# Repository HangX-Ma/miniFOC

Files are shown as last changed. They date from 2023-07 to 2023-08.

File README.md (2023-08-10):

# miniFOC

This repository records my development of miniFOC. You can obtain the source files of the hardware and software in this repository.

## Introduction

This FOC driver board has three control mode, _Torque_, _Velocity_, _Angle_. You can control the motor accurately and smoothly using _**Voltage Control**_, because I haven't solved the _**Current Loop Control**_ problem.

Vofa+ can be used to control the motor conveniently. I also design a group of virtual keys to test the menu UI. You can find Vofa+ command configuration [vofa+.cmds.json](/Software/foc/vofa+.cmds.json) and [foc_debugger.tab.json](/Software/foc/foc_debugger.tab.json) that can assist you build up your debug platform quickly.

I have added a `Torque Ratchet Mode` under torque control. You can have a try.

> **NOTE:** <span style="color: #98C379; font-weight: bold;">`Software/foc/foc.ioc`</span> is only used for configuration reference.
>
> **NOTE:** :heavy_exclamation_mark: The hardware design is immature, which has some line sequence mistakes.

You can check the pin set via [cubemx-settings](assets/cubemx-settings.png). Vofa+ debugger tab can also be found in [assets/vofaplus.png](assets/vofaplus.png).

<div align="center">
    miniFOC design(concept), HangX-Ma
    <br>
    <font size="2" color="#999"><u>miniFOC design(concept), HangX-Ma</u></font>
    <br>
    <br>
</div>

<div align="center">
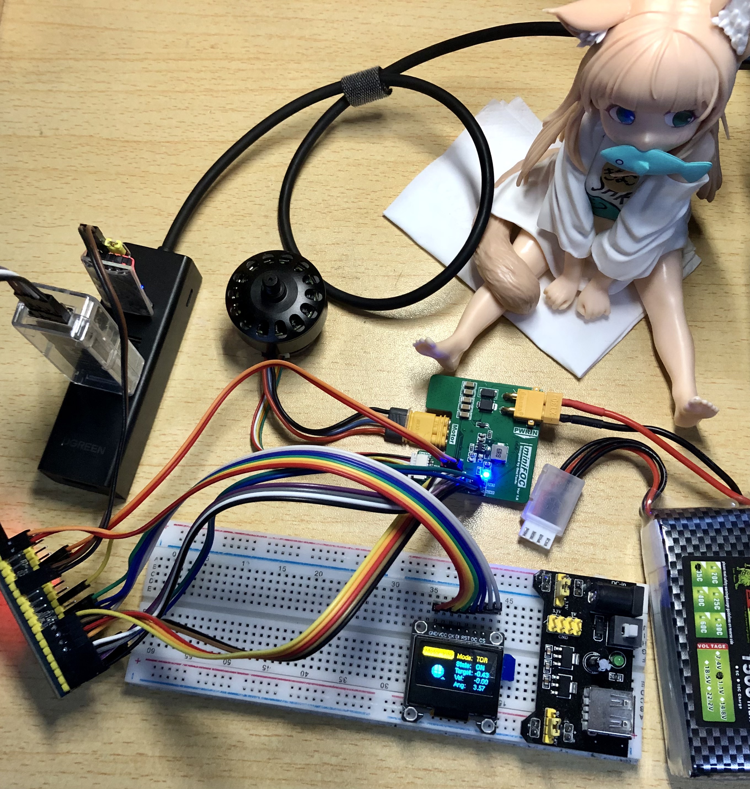
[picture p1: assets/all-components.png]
FOC board and other components, HangX-Ma
    
    <br>
    <font size="2" color="#999"><u>FOC board and other components, HangX-Ma</u></font>
    <br>
    <br>
</div>

> I will try to use sensor-less control strategy if the fundamental functions all perform well.

## Driver Parameters

| Item | Value |
| :---: | :---: |
| Input voltage range | 8 V ~ 40 V |
| Maximum current | 1.5 A |
| Serial port baud rate | 115200 |
| MCU | STM32F103C8T6, 64 KB flash, 20 KB RAM |
| OLED | SSD1306, 128 x 64, 7 wires SPI |
| Motor | 2808, KV900, 12 V|

## Environment

- **Serial Port Tool:** [Vofa+](https://www.vofa.plus/downloads/?v=7/17/2023)
- **OLED UI:** [WouoUI](https://github.com/RQNG/WouoUI), [uYanki/menu](https://github.com/uYanki/board-stm32f103rc-berial/tree/main/7.Example/hal/gui/u8g2/02_menu)
- **Dev Tools:** VSCode, CMake, OpenOCD, STLInk-v2, CMSIS-DAPv2, STM32CubeMX
- **Debugger:** Cortex-Debug
- **Library:** [u8g2](https://github.com/olikraus/u8g2), [Qfplib-M3](https://www.quinapalus.com/qfplib-m3.html)

## Features

- [x] Using space vector pulse width modulation
- [x] Torque control without current sensor
- [x] Rotational speed closed loop control
- [x] Rotation angle closed loop control
- [ ] Torque control with current sensor
- [x] Smooth UI that can be controlled by virtual keys currently via Vofa

## FOC Application

- _**Torque Normal Mode**_

    &emsp;&emsp; Under torque control, you can set the `target torque` and `Kp` to adjust torque feedback force.

- _**Torque Ratchet Mode**_

    &emsp;&emsp; Under torque control, the motor will act like a ratchet.

    &emsp;&emsp; You can change `Kp` to adjust the stiffness.

- _**Torque Rebound Mode**_

    &emsp;&emsp; Under torque control, the motor will rebound to the specific angle.

    &emsp;&emsp; You can set the angle or change the rebound force by adjusting the `Kp` value.

- _**Torque Damp Mode**_

    &emsp;&emsp; Under torque control, the motor will act like a knob with damp.

    &emsp;&emsp; If you increase the `target torque` value, the damp will increase.

    &emsp;&emsp; If you increase the `Kd` value, the knob will become smoother.

## Problem Found

- SPI output pins sequence needs to be `CS`, `SCLK`, `MISO`, `MOSI`.
- Magnetic attached to motor will affect the motor itself, my friend suggests me to use sensorless control strategy.
- More power ports need to be reserved, such as `GND`, `3V3`.
- SPI OLED ports sequence needs to be `GND`, `VCC`, `SCK`, `MOSI`, `RST`, `DC`, `CS`.
- `nFault` pin of the DRV8313 needs to be controlled and monitored by the MCU. Currently, only unplugging battery can release the DRV8313 off the fault state.

## Development Logs

### 2023-08-10

- Fix the problem caused by TIM3 configuration, which will lead to OLED abnormal display.
    > I remove the `LL_TIM_CC_EnableChannel` function, which actually used in capture/compare mode! It is a coincidence that the OLED pins happened to be coincided with the configured channel.
- Change current sampling to three phases version.
- Move FOC state update in ADC1 DMA transfer complete interrupt. This will fit the current sampling demand and meet the inner ring frequency requirements.
- Current sensors are combined with a strange 100 Hz sine- wave noise. I cannot fix it currently.

<div align="center">
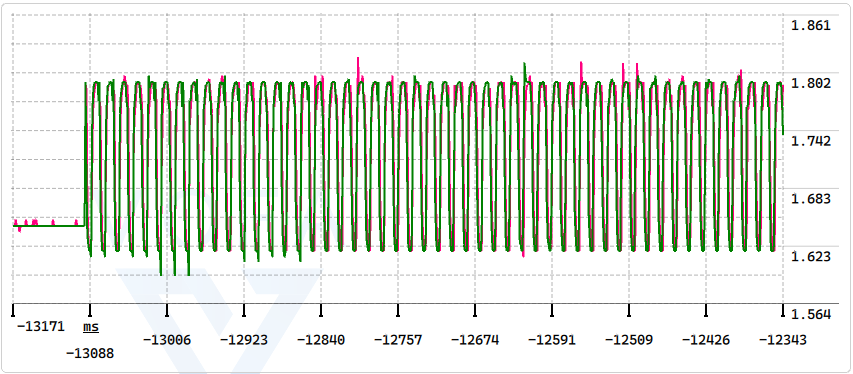
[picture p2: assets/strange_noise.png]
Strange 100 Hz sine-wave current noise , HangX-Ma
    
    <br>
    <font size="2" color="#999"><u>Strange 100 Hz sine-wave current noise
, HangX-Ma</u></font>
</div>

### 2023-08-06 to 2023-08-07

- Reconstruct GUI logic to support mult-level menu and motor app mode switch.
- Enhance the MainUI animation logic to follow the actual angle position.
- Add **Damp Mode**.
- Add damp feeling control for **Rebound Mode**
- Add _**High Pass Filter**_ but it is discarded afterwards because it filters out the useful information.

### 2023-08-05

- Update the voltage control with with current estimation and Back-EMF compensation. I take a reference to SimpleFOC, [Torque control using voltage](https://docs.simplefoc.com/voltage_torque_mode).

<div align="center">
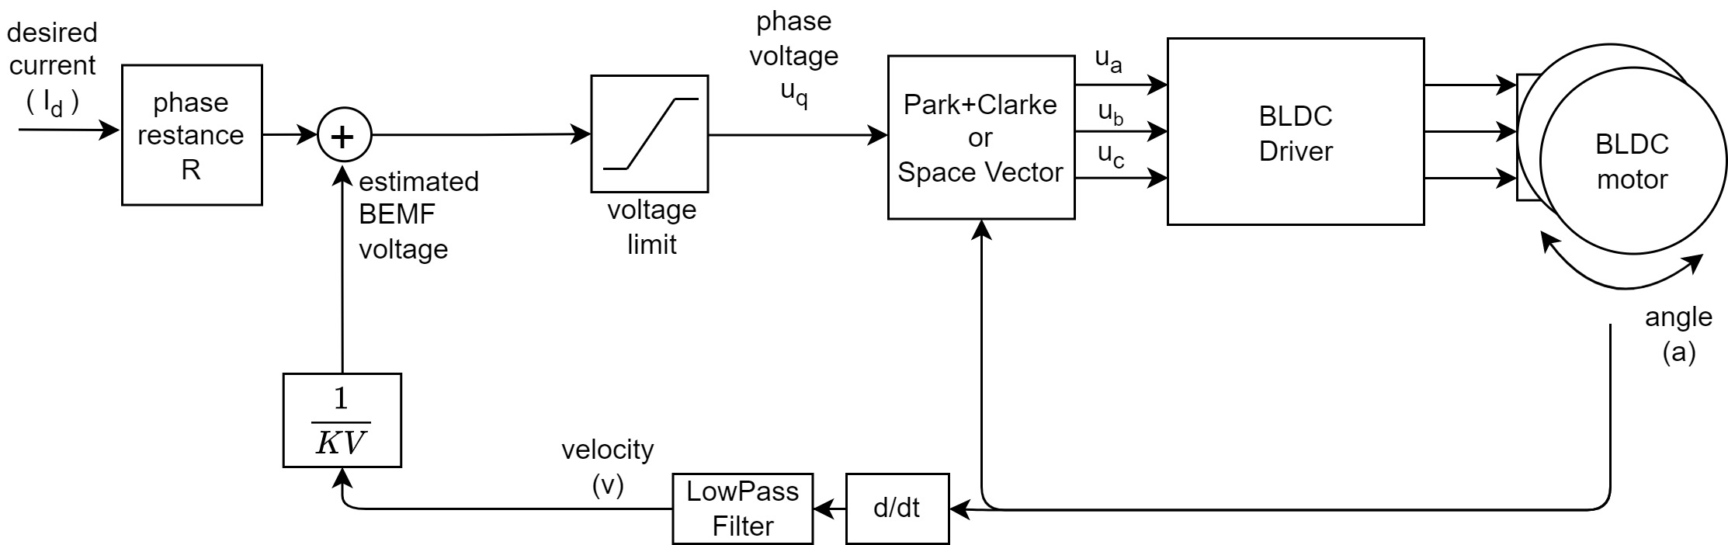
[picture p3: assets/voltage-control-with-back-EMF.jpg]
Voltage control with current estimation and Back-EMF compensation , HangX-Ma
    
    <br>
    <font size="2" color="#999"><u>Voltage control with current estimation and Back-EMF compensation
, HangX-Ma</u></font>
</div>

### 2023-08-01 to 2023-08-04

- Add OLED smooth menu UI and make control relationship between UI and motor. The motor information such that **Motor Control Mode**, **Motor State**, **Control Target**, **Shaft Velocity**, **Shaft Angle**. The animation in _MainUI_ will show you the state of motor!

### 2023-07-31

- Find a project procedure problem that you must reconfirm the encoder direction if you reassemble your hardware.
- Only low speed mode can support the motor position rebound test. Otherwise, the motor will be damaged.
    > :sob: My motor seems to be damaged. (Update: It recovered!)
- Replace the PWMA current sensor and the current loop start to work.
    > I finally only give Q and D with Kp = 0.6 and make the current loop work. But actually current loop version performs not as good as non current loop version.
- Torque needs to be greater than 0.6 under current loop control.
- Add ratchet mode under torque control.

### 2023-07-30

- Add current sense monitor feedback, thus, creating a current control loop.
    > :x: Current phase sequence is necessary to be identified. I haven't solve the it. Motor can not work when current feedback added.
- Add _Torque Control_ part, reconstruct the control logic and delete some abundant codes.

### 2023-07-29

- Add velocity control loop and fix the jitter problem.
- Add position control loop.
- Add motion switch function and fix the motor jump problem when control type switches.
- Remove integral part in _Angle Control_. Only proportional part is left.
    > :heavy_exclamation_mark: Integral part actually causes serious overshoot problem and affects the system response speed.

### 2023-07-28

- Attach the magnetic with shaft sleeve, sticking it on the shaft.
- Remake an encoder board because previous one seems to be damaged.
- Ensure the UVW sequence of the Motor.
- <span style="color: #98C379; font-weight: bold;">[Pass TEST3]:</span> Open loop position control test passes.
- Add `printf` redirection code.
- Add sensor alignment code: Identify the sensor direction, pole pairs and calculate the zero electrical angle offset.
    > The code will be trapped into a rabbit hole if the motor rotates not fluently. So check the serial output first!

### 2023-07-26

- Add OLED menu base code.

### 2023-07-25

- INA199x1 has been configured successfully. I use TIM3 to generate update event to trigger ADC1 to start multi-channel conversion. The conversion result will be carried by DMA and send to specific address.
- Add `get_RS_current` function that can conveniently return the rotor and stator current (Id and Iq). I also write a test code for it.

### 2023-07-24

- SC60228DC magnetic encoder works well. I brought _5 mm x 2 mm (d x h)_ magnetic but can not stick it to the motor bearing using hot-melt adhesive. I will use AB glue instead.
    > Waiting for essential materials again~

### 2023-07-23

- Add SVPWM control module and change PWM to center aligned mode.
- <span style="color: #98C379; font-weight: bold;">[Pass TEST2]:</span> SVPWM control test passes.

### 2023-07-22

- <span style="color: #98C379; font-weight: bold;">[Pass TEST1]:</span> Direct given PWM can successfully drive BLDC motor.
- Fix transmission error of SPI2, which is linked to magnetic encoder. But I forget to buy the magnetic, so fully check hasn't been done.

### 2023-07-21

- Add [u8g2](https://github.com/olikraus/u8g2) OLED library and add OLED demo code.
    >
    > - :x: OLED can not display normally, which needs further checking.
    > - :heavy_check_mark: Remove SPI1 DMA and the SPI OLED can display normally using u8g2.

- Reconstruct PWMx configurations and merges it into BLDC configurations.
- Add BLDC motor tests for checking different BLDC motor working conditions.
- Add USART control to start or stop BLDC motor.
- Driver board has been prepared.

### 2023-07-19

- Add [Qfplib-M3](https://www.quinapalus.com/qfplib-m3.html) float-point library and it works well!
    > I use cortex-debug plugin and it shows that Qfplib-M3 is visibly faster than software float-point calculation.
- Add Vofa+ communication protocol and configure USART1.
    >
    > - :question: Cough... It seems that my CH340 serial communication device breaks down. Need further checking.
    > - :heavy_check_mark: I use logic analyzer to capture output of _**PB6(Tx)**_ and it actually gives me different waveforms, which means that the CH340 is actually broken.

### 2023-07-18

- Change SPI mode to **(Receive Only Master)** and finish the SC60228DC software logic.
    > Use OOP concept to write SC60228DC, use method in `g_encoder` can satisfy the user's need.

### 2023-07-17

- :book: Create a mind map about _miniFOC_ design.
- :rocket: Finish the board design but haven't check the details. Prepare for further checking and BOM selections.
    > :heavy_check_mark: BOM and board have been checked. Waiting for all materials to arrive.
- Remove `TIM1_CH1N`, `TIM1_CH2N`, `TIM1_CH3N` settings， because they are not used in this driver.

### 2023-07-15

- :x: I tried to use proteus 8.15 to develop the software using online simulation, but the NMOS in proteus performed abnormally. I will use **Logic Analyzer** instead and design the modular board.

## License

Apache License Version 2

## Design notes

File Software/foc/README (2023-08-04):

# SPDX-License-Identifier: Apache-2.0
# (C) Copyright 2023
# HangX-Ma, contour.9x@gmail.com

Warning:
========

1. Don't use the 'Makefile' in the root directory. It is generated
   by STM32CubeMX, which is not maintained.

2. Don't use the STM32CubeMX directly. It only gives you a reference
   to my configurations.

3. Only low speed mode can support the motor position rebound test.
   Otherwise, the motor will be damaged.

Note:
========

1. Wait until the LED off and then start the motor. Otherwise, you
   may cause an undefined situation.

2. If the motor suddenly stops, it may be now protected by the DRV8313,
   you need to pull off the battery to release the fault state of DRV8313.

3. Torque needs to be greater than 0.6 under current loop control

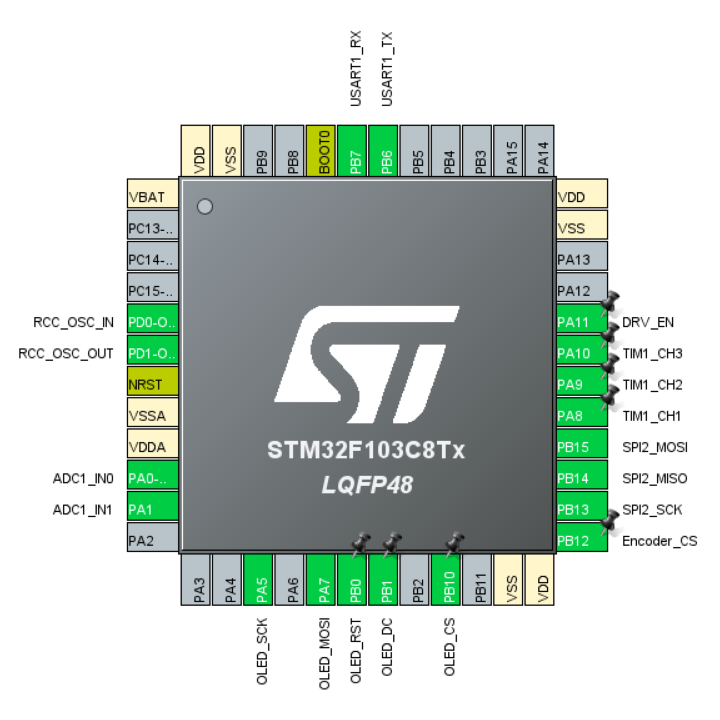
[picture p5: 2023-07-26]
assets/cubemx-settings.png

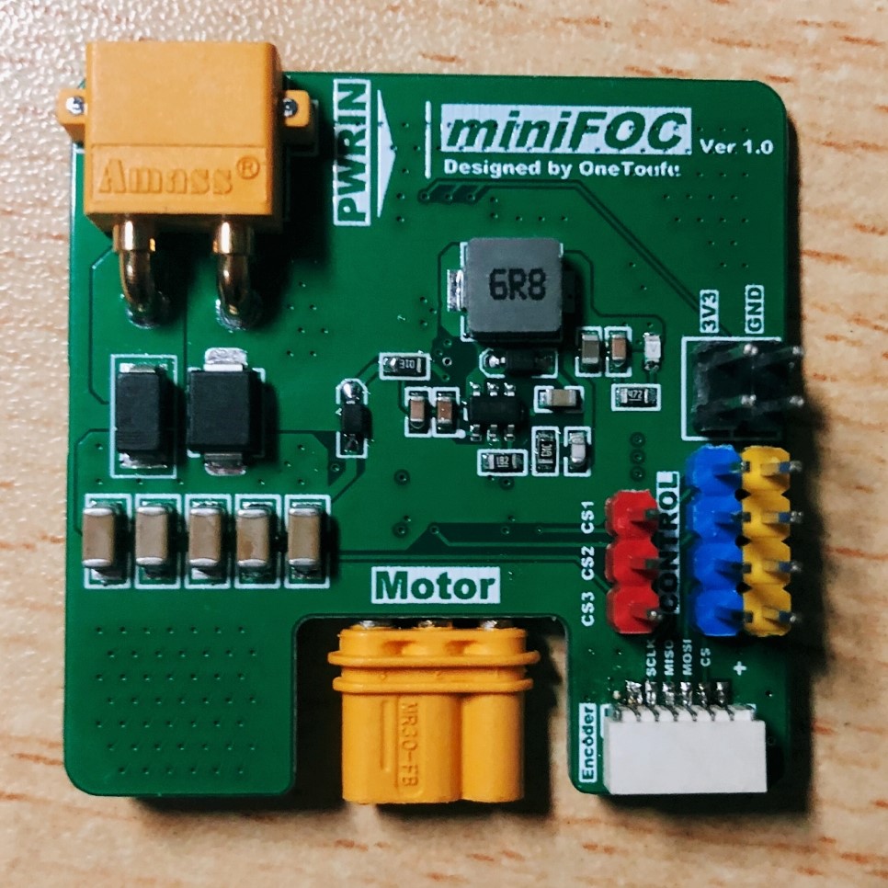
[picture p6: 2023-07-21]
assets/bldc-board.png

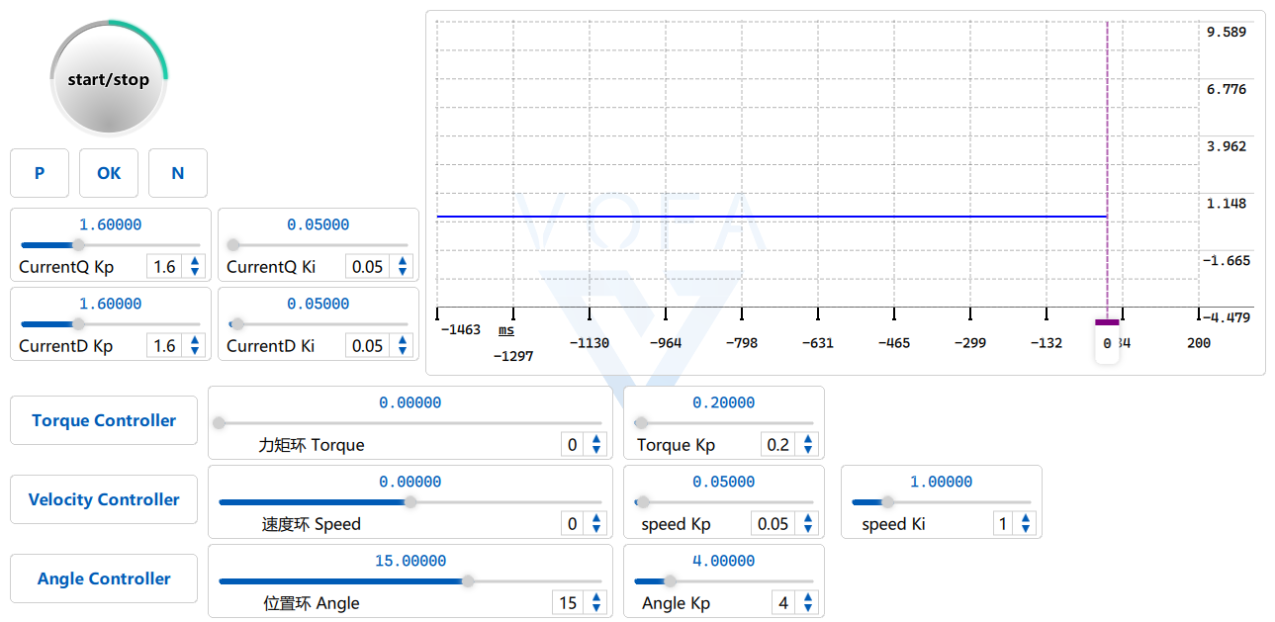
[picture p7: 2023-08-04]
assets/vofaplus.png

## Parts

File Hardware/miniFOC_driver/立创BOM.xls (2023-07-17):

购买类型 | 商品编号 | 物料编码 | 商品分类 | 名称 | 商品型号 | 品牌 | 封装规格 | 单个毛重 | 购买数量 | 商品单价 | 金额
常规 | C431092 |  | 插头 | AMASS(艾迈斯)航模插头 卧式弯脚 XT30PW-M公头 袋装 | XT30PW-M | AMASS(艾迈斯) | - | 0.001296000 | 3 | ￥2.22 | ￥6.66
常规 | C30926 |  | 贴片电容(MLCC) | 100nF ±10% 50V 编带 | 0603B104K500NT | FH(风华) | 0603 | 0.000030000 | 100 | ￥0.014054 | ￥1.41
常规 | C77572 |  | 贴片电容(MLCC) | 470nF ±10% 50V 编带 | 0603B474K500NT | FH(风华) | 0603 | 0.000030000 | 50 | ￥0.092223 | ￥4.61
常规 | C14665 |  | 贴片电容(MLCC) | 100pF ±5% 50V 编带 | CC0603JRNPO9BN101 | YAGEO(国巨) | 0603 | 0.000029000 | 100 | ￥0.013901 | ￥1.39
常规 | C100042 |  | 贴片电容(MLCC) | 10nF ±10% 50V 编带 | CC0603KRX7R9BB103 | YAGEO(国巨) | 0603 | 0.000023000 | 100 | ￥0.012596 | ￥1.26
常规 | C96446 |  | 贴片电容(MLCC) | 10uF ±20% 25V 编带 | CL10A106MA8NRNC | SAMSUNG(三星) | 0603 | 0.000035000 | 20 | ￥0.148527 | ￥2.97
常规 | C883598 |  | 贴片电容(MLCC) | 100uF ±20% 10V 编带 | GRM31CR61A107MEA8L | muRata(村田) | 1206 | 0.000045000 | 10 | ￥1.2912 | ￥12.91
常规 | C2929944 |  | 肖特基二极管 | SS54 编带 | SS54 | CJ(江苏长电/长晶) | SMAG | 0.000500000 | 5 | ￥0.598284 | ￥2.99
常规 | C726872 |  | 瞬态抑制二极管(TVS) | SMBJ28CA 编带 | SMBJ28CA | TWGMC(台湾迪嘉) | SMB(DO-214AA) | 0.000152000 | 10 | ￥0.211826 | ￥2.12
常规 | C22624 |  | 肖特基二极管 | 40V 1A 600mV@1A 编带 | B5819WS | CJ(江苏长电/长晶) | SOD-323 | 0.000029000 | 20 | ￥0.186073 | ￥3.72
常规 | C325965 |  | 功率电感 | 6.8uH ±20% 编带 | SLO0530H6R8MTT | Sunltech(韩国顺磁) | SMD | 0.000340000 | 5 | ￥0.838292 | ￥4.19
常规 | C99873 |  | 插头 | AMASS(艾迈斯)锂电池三芯电源连接器公头MR30-M 2件套 袋装 | MR30-M | AMASS(艾迈斯) | - | 0.001950000 | 2 | ￥1.79 | ￥3.58
常规 | C23162 |  | 贴片电阻 | 厚膜电阻 4.7kΩ ±1% 100mW 编带 | 0603WAF4701T5E | UNI-ROYAL(厚声) | 0603 | 0.000023000 | 100 | ￥0.006624 | ￥0.66
常规 | C4177 |  | 贴片电阻 | 厚膜电阻 1.8kΩ ±1% 100mW 编带 | 0603WAF1801T5E | UNI-ROYAL(厚声) | 0603 | 0.000023000 | 100 | ￥0.006187 | ￥0.62
常规 | C25804 |  | 贴片电阻 | 厚膜电阻 10kΩ ±1% 100mW 编带 | 0603WAF1002T5E | UNI-ROYAL(厚声) | 0603 | 0.000023000 | 100 | ￥0.005512 | ￥0.55
常规 | C136593 |  | 贴片电阻 | 1MΩ ±1% 100mW 编带 | RS-03K1004FT | FH(风华) | 0603 | 0.000030000 | 100 | ￥0.004880 | ￥0.49
常规 | C728271 |  | 贴片电阻 | 10mΩ ±1% 500mW 编带 | PA0805FRE470R01L | YAGEO(国巨) | 0805 | 0.000030000 | 10 | ￥0.368704 | ￥3.69
常规 | C92482 |  | 电机驱动芯片 | 无刷直流BLDC电机驱动芯片 60V 编带 | DRV8313PWPR | TI(德州仪器) | TSSOP-28-EP | 0.000261000 | 2 | ￥13.08 | ￥26.16
常规 | C97643 |  | DC-DC电源芯片 | 降压型 编带 | ME3116AM6G | MICRONE(南京微盟) | SOT-23-6 | 0.000055000 | 5 | ￥0.8500 | ￥4.25
常规 | C59135 |  | 电流感应放大器 | INA199A1DCKR 编带 | INA199A1DCKR | TI(德州仪器) | SOT-323-6 | 0.000070000 | 10 | ￥1.99 | ￥19.90

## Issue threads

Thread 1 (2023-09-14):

Hello

Candas1, 2023-09-14:
Hello,

Very insteresting project.
Are you in the SimpleFOC community ?
I am currently checking if Qfplib would help getting FOC to run faster and just saw you are using it.
Do you have any feedback ?

Thanks in advance.

HangX-Ma, 2023-09-14:
I'm glad you are interested in my miniFOC project. I'm not a member of Simple FOC community but I actually learn a lot techniques and knowledge from it. I once majored in EE when in undergraduate. Doing this project was purely out of personal interest. Qfplib works well in Cortex-M3 series chips. I think TI's IQmath has widely used in such chips that has no hardware float calculation capability. I just want to find a math library to substitute it. Actually, Qfplib works well. I used to debug my project and this math library visibly speeded up the calculation process, though not accurately as using those timing lib. I hope my answer can assist your further study and work. -v-

Candas1, 2023-09-15:
Thank you.
I will try it, it seems Qfplib can be used to substitute match operators without changing the code ([blog post](https://lupyuen.github.io/articles/stm32-blue-pill-shrink-your-math-libraries-with-qfplib)).

I recently proposed [this](https://github.com/simplefoc/Arduino-FOC/pull/309), maybe this is also useful for you.

SimpleFOC could probably run on your hardware.

HangX-Ma, 2023-09-15:
Great posts! Thanks for your suggestion. I think they will increase my understanding of Qfplib and optimize my firmware.

Candas1, 2023-09-18:
You have 3 shunts, you could also only use the 2 phase currents of the phases with lowest duty cycle and do the foc with 2 phase currents only.

That would prevent issues at high duty cycle.

HangX-Ma, 2023-09-18:
> You have 3 shunts, you could also only use the 2 phase currents of the phases with lowest duty cycle and do the foc with 2 phase currents only.
>
> That would prevent issues at high duty cycle.

I used to use the two phases version, but I encountered with the current phase sequence problem. Three phases control version cloud give me a chance to change the current phase sequence conveniently. Finally, I found that maybe my hardware design has some subtle mistakes that introduces noise into the current sense module. I didn't solve this problem. So this firmware version only uses the voltage control method.

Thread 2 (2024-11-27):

Interest with your project posible step/dir input??

artayasa, 2024-11-27:
Hi mate i want make this, i have all, but i want make a high power, i have it with opto isolated. But it need pwm for hin and lin active low. Is posible??

artayasa, 2024-11-30:
> > Hi mate i want make this, i have all, but i want make a high power, i have it with opto isolated. But it need pwm for hin and lin active low. Is posible??
>
> Hi, I haven't tested this board limitation. But I think this project may not suitable because the motor current may overflow the tolerance value. And drv8313 may be not a good choice for high power situation.

Owhh is still used drv ohh ok

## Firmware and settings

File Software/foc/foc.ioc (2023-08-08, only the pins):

Mcu.UserName=STM32F103C8Tx
PA0-WKUP.Signal=ADCx_IN0
PA1.Signal=ADCx_IN1
PA10.Signal=S_TIM1_CH3
PA11.GPIO_Label=DRV_EN
PA11.Signal=GPIO_Output
PA2.Signal=ADCx_IN2
PA5.GPIO_Label=OLED_SCK
PA5.Signal=SPI1_SCK
PA7.GPIO_Label=OLED_MOSI
PA7.Signal=SPI1_MOSI
PA8.Signal=S_TIM1_CH1
PA9.Signal=S_TIM1_CH2
PB0.GPIO_Label=OLED_RST
PB0.Signal=GPIO_Output
PB1.GPIO_Label=OLED_DC
PB1.Signal=GPIO_Output
PB10.GPIO_Label=OLED_CS
PB10.Signal=GPIO_Output
PB12.GPIO_Label=Encoder_CS
PB12.Signal=GPIO_Output
PB13.Signal=SPI2_SCK
PB14.Signal=SPI2_MISO
PB15.Signal=SPI2_MOSI
PB6.Signal=USART1_TX
PB7.Signal=USART1_RX
PD0-OSC_IN.Signal=RCC_OSC_IN
PD1-OSC_OUT.Signal=RCC_OSC_OUT

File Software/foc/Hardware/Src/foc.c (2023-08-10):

#include "foc.h"
#include "foc_app.h"
#include "config.h"
#include "bldc_config.h"
#include "encoder.h"
#include "qfplib-m3.h"
#include "vofa_usart.h"
#include "led.h"
#include "pid.h"
#include <math.h>
#include "current_monitor.h"

#include "stm32f1xx_ll_utils.h"
#include "stm32f1xx_ll_tim.h"

FOC g_foc;

// normalize angle to range [0, 2PI]
static float normalize_angle(float angle) {
    float _fmod = fmodf(angle, _2PI);
    return _fmod >= 0 ? _fmod : qfp_fadd(_fmod, _2PI);
}

static float get_electrical_angle(float shaft_angle) {
    return normalize_angle(
        qfp_fsub(
            qfp_fmul(shaft_angle, (float)g_foc.property_.pole_pairs),
            g_foc.property_.zero_electrical_angle_offset
        )
    );
}


static void set_phase_voltage(float Uq, float Ud, float e_angle) {
    float U_ref, U_alpha, U_beta;
    float T0, T1, T2;
    float Ta, Tb, Tc;
    uint8_t sector;

    // invert park
    U_alpha = qfp_fsub(qfp_fmul(Ud, qfp_fcos(e_angle)), qfp_fmul(Uq, qfp_fsin(e_angle)));
    U_beta  = qfp_fadd(qfp_fmul(Ud, qfp_fsin(e_angle)), qfp_fmul(Uq, qfp_fcos(e_angle)));

    // normalized U_ref range between [-1, 1]
    U_ref = qfp_fdiv(qfp_fsqrt(qfp_fadd(qfp_fmul(U_alpha, U_alpha), qfp_fmul(U_beta, U_beta))), MOTOR_VM);

    // We need to calculate the rotor's electric angle. THe rotor is _PI_2 head of the stator.
    if (Uq > 0) {
        e_angle = normalize_angle(qfp_fadd(e_angle, _PI_2));
    } else {
        e_angle = normalize_angle(qfp_fsub(e_angle, _PI_2));
    }

    // SVPWM maximum distortion-free rotation voltage vector: sqrt(3)/3
    // The inscribed circle of a hexagon.
    if (U_ref > 0.577f) {
        U_ref = 0.577f;
    }
    if (U_ref < -0.577f) {
        U_ref = -0.577f;
    }

    // calculate the sector
    sector = (uint8_t) qfp_fdiv(e_angle, _PI_3) + 1;

    // calculate the neighbour voltage vector action time

    float m = qfp_fmul(_SQRT3, U_ref);
    T1 = qfp_fmul(m, qfp_fsin(qfp_fsub(qfp_fmul(sector, _PI_3), e_angle)));
    T2 = qfp_fmul(m, qfp_fsin(qfp_fsub(e_angle, qfp_fmul(qfp_fsub(sector, 1.0f), _PI_3))));
    T0 = qfp_fsub(qfp_fsub(1.0f, T1), T2);

    float T0_2 = qfp_fdiv(T0, 2.0f);

    switch(sector)
    {
        case 1:
            Ta = qfp_fadd(qfp_fadd(T1, T2), T0_2);
            Tb = qfp_fadd(T2, T0_2);
            Tc = T0_2;
            break;
        case 2:
            Ta = qfp_fadd(T1, T0_2);
            Tb = qfp_fadd(qfp_fadd(T1, T2), T0_2);
            Tc = T0_2;
            break;
        case 3:
            Ta = T0_2;
            Tb = qfp_fadd(qfp_fadd(T1, T2), T0_2);
            Tc = qfp_fadd(T2, T0_2);
            break;
        case 4:
            Ta = T0_2;
            Tb = qfp_fadd(T1, T0_2);
            Tc = qfp_fadd(qfp_fadd(T1, T2), T0_2);
            break;
        case 5:
            Ta = qfp_fadd(T2, T0_2);
            Tb = T0_2;
            Tc = qfp_fadd(qfp_fadd(T1, T2), T0_2);
            break;
        case 6:
            Ta = qfp_fadd(qfp_fadd(T1, T2), T0_2);
            Tb = T0_2;
            Tc = qfp_fadd(T1, T0_2);
            break;
        default:  // possible error state
            Ta = 0.0f;
            Tb = 0.0f;
            Tc = 0.0f;
    }
    g_bldc.set_pwm_a_duty((uint32_t)qfp_fmul(Ta, (float)PWM_RELOAD_PERIOD));
    g_bldc.set_pwm_b_duty((uint32_t)qfp_fmul(Tb, (float)PWM_RELOAD_PERIOD));
    g_bldc.set_pwm_c_duty((uint32_t)qfp_fmul(Tc, (float)PWM_RELOAD_PERIOD));
}

// Encoder DIR needs to be reserved. Otherwise, the FOC will stick into one
// position if you call any function that rely on the encoder feedback.
#define ESTIMATE_ENCODER_DIR    (1)
static void align_sensor(void) {
    // electrical direction needs to be correspond to the mechanical angle
    float e_angle; // electrical angle
    float forward_angle, back_angle, delta_abs_angle; // mechanic angle

    printf("\n[Motor]: Start sensor alignment...\r\n");

    // we need to start pwm output first
    LED_STATE_ON();
    g_bldc.start_pwm();
    LL_mDelay(500);

    /* We want to ensure the sensor direction and the pole pairs number */
    // forward 2PI electrical angle
    for(int i = 0; i <= 100; i++) {
        e_angle = qfp_fadd(_3PI_2, qfp_fdiv(qfp_fmul(_2PI, i), 100.0f));
        g_foc.set_phase_voltage(SENSOR_ALIGN_VOLTAGE, 0, e_angle);
        LL_mDelay(20);
    }
    forward_angle = g_encoder.get_angle();

    // turn back
    for(int i = 100; i >= 0; i--) {
        e_angle = qfp_fadd(_3PI_2, qfp_fdiv(qfp_fmul(_2PI, i), 100.0f));
        g_foc.set_phase_voltage(SENSOR_ALIGN_VOLTAGE, 0, e_angle);
        LL_mDelay(20);
    }
    back_angle = g_encoder.get_angle();

    printf("[Motor]: Forward angle is degree %d\r\n", (int)qfp_fmul(qfp_fdiv(forward_angle, _PI), 180.0f));
    printf("[Motor]: Back angle is degree %d\r\n", (int)qfp_fmul(qfp_fdiv(back_angle, _PI), 180.0f));

    // Try to stop motor at zero point
    g_foc.set_phase_voltage(0, 0, 0);
    LL_mDelay(200);

    // Motor moves none, which indicates motor error.
    delta_abs_angle = abs(qfp_fsub(forward_angle, back_angle));
    if(( delta_abs_angle < 0.02f)) {
        printf("[Motor]: Abnormal state. Please check encoder or motor.\n");
        LED_STATE_OFF();
        // stop pwm output. Motor will be stopped and this also can avoid emergency situation
        g_bldc.stop_pwm();
        return;
    }

#if ESTIMATE_ENCODER_DIR
    //* determine the sensor direction
    if(forward_angle < back_angle) {
        printf("[Motor]: Encoder dir is CCW\r\n");
        g_encoder.dir_ = CCW;
    }
    else {
        printf("[Motor]: Encoder dir is CW\r\n");
        g_encoder.dir_ = CW;
    }
#else
    g_encoder.dir_ = CCW;
#endif

#if ESTIMATE_POLE_PAIRS
    //* calculate motor pole pairs
    printf("[Motor]: Pole pairs checking...\r\n");
    // 0.5 is arbitrary number it can be lower or higher!
    // If the default pole pairs isn't correct, we use the calculated one!
    if( abs(qfp_fsub(qfp_fmul(delta_abs_angle, g_foc.property_.pole_pairs), _2PI)) > 0.5f ) {
        g_foc.property_.pole_pairs = qfp_fadd(qfp_fdiv(_2PI, delta_abs_angle), 0.5f);
        if (g_foc.property_.pole_pairs > MOTOR_POLE_PAIRS + 1 || g_foc.property_.pole_pairs < MOTOR_POLE_PAIRS - 1) {
            g_foc.property_.pole_pairs = MOTOR_POLE_PAIRS;
            printf("[Motor]: Estimate pole pairs error.\n");
            LED_STATE_OFF();
            // stop pwm output. Motor will be stopped and this also can avoid emergency situation
            g_bldc.stop_pwm();
            return;
        } else {
            printf("[Motor]: Estimated pole pairs = %d\r\n", g_foc.property_.pole_pairs);
        }
    } else {
        printf("[Motor]: Ok!\r\n");
    }
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

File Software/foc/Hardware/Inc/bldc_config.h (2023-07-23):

/**
 * @file bldc_config.h
 * @author HangX-Ma (contour.9x@gmail.com)
 * @brief BLDC essential configurations
 * @version 0.1
 * @date 2023-07-21
 * @ref https://github.com/simplefoc/Arduino-FOC-drivers/tree/master/src/encoders/sc60228
 * @ref https://blog.csdn.net/weixin_43593122/article/details/119253544
 *
 * @copyright Copyright (c) 2023
 *
 * Licensed under the Apache License, Version 2.0 (the "License");
 * you may not use this file except in compliance with the License.
 * You may obtain a copy of the License at
 *
 *    http://www.apache.org/licenses/LICENSE-2.0
 *
 * Unless required by applicable law or agreed to in writing, software
 * distributed under the License is distributed on an "AS IS" BASIS,
 * WITHOUT WARRANTIES OR CONDITIONS OF ANY KIND, either express or implied.
 * See the License for the specific language governing permissions and
 * limitations under the License.
 */

#ifndef __BLDC_CONFIG__H__
#define __BLDC_CONFIG__H__

#include "utils.h"

#define BLDC_DRV_EN_GPIO_PORT       GPIOA
#define BLDC_DRV_EN_PIN             LL_GPIO_PIN_11

#define BLDC_PWMx_GPIO_PORT         GPIOA
#define BLDC_PWMA_PIN               LL_GPIO_PIN_8
#define BLDC_PWMB_PIN               LL_GPIO_PIN_9
#define BLDC_PWMC_PIN               LL_GPIO_PIN_10

typedef struct BLDC {
    void (*set_pwm_a_duty)(uint32_t);
    void (*set_pwm_b_duty)(uint32_t);
    void (*set_pwm_c_duty)(uint32_t);
    void (*start_pwm)(void);
    void (*stop_pwm)(void);
} BLDC;
extern BLDC g_bldc;

void bldc_init();

#endif  //!__BLDC_CONFIG__H__

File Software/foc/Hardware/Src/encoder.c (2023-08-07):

#include "encoder.h"
#include "delay.h"
#include "qfplib-m3.h"
#include "pid.h"

#include "stm32f1xx_ll_utils.h"
#include "stm32f1xx_ll_spi.h"
#include "stm32f1xx_ll_gpio.h"
#include "stm32f1xx_ll_bus.h"


Encoder g_encoder;
typedef struct {
    BOOL error_check;   // indicate the SC60228 state
    BOOL parity_check;  // if the received data has error or not
} data_check_t;

static data_check_t data_check = {
    .error_check = FALSE,
    .parity_check = FALSE,
};


static float raw_angle_data_prev = 0; // last raw angle value, MAX = ENCODER_RESOLUTION
static float angle_prev = 0; // last angle value(radian)
static float rotation_turns_angles = 0; // how may turns the motor runs(radian)

static uint16_t spi2_transmit_rw(uint16_t outdata) {
    // wait until the SPI Tx buffer to be empty
    while (LL_SPI_IsActiveFlag_TXE(SPI2) == RESET) {}
    LL_SPI_TransmitData16(SPI2, outdata);
    // wait for 16 bits data receiving complete
    while (LL_SPI_IsActiveFlag_RXNE(SPI2) == RESET) {}
    return LL_SPI_ReceiveData16(SPI2);
}

static void select_chip(void) {
    LL_GPIO_ResetOutputPin(ENCODER_GPIO_PORT, ENCODER_CS_PIN);
    // min delay 250 ns
    delay_nus_72MHz(2);
}

static void deselect_chip(void) {
    // min delay here: clock period / 2, our baud rate period is 222ns
    delay_nus_72MHz(2);
    LL_GPIO_SetOutputPin(ENCODER_GPIO_PORT, ENCODER_CS_PIN);
    // min delay until next read: 250ns
    delay_nus_72MHz(2);
}

static BOOL is_error(void) {
    return data_check.error_check;
}

static BOOL is_valid(void) {
    return data_check.parity_check;
}

/**
 * @brief Check parity
 * @param data data needs to be checked
 * @return if the number of '1' is odd, return '1', else return '0'
 * @ref https://blog.csdn.net/ftswsfb/article/details/104321901
 */
static BOOL parity_check(uint16_t data)
{
    BOOL parity = RESET;
    while (data) {
        parity = !parity;
        data &= data - 1;
    }
    return parity;
}

static uint16_t read_raw_angle(void) {
    SC60228Angle result;
    select_chip();
    result.reg = spi2_transmit_rw(0x0000);
    deselect_chip();
    data_check.error_check = (result.err == 1);
    data_check.parity_check = parity_check(result.angle);

    return result.angle;
}

static float get_angle(void) {
    uint8_t count = 0;
    float raw_angle_data = read_raw_angle();
    // invalid angle is a small probability event
    while (!is_valid() && count < 2) {
        raw_angle_data = read_raw_angle();
        count++;
    }

    float d_raw_angle = raw_angle_data - raw_angle_data_prev;
    // record the whole turns angles(according to d_raw_angle's direction)
    if(abs(d_raw_angle) > qfp_fmul(0.8, (float)ENCODER_RESOLUTION)) {
        rotation_turns_angles = qfp_fadd(d_raw_angle > 0 ? -_2PI : _2PI, rotation_turns_angles);
    }
    raw_angle_data_prev = raw_angle_data;
    // return current angle(rad)
    return qfp_fadd(qfp_fmul(qfp_fdiv(raw_angle_data, (float)ENCODER_RESOLUTION), _2PI), rotation_turns_angles);
}

static float get_shaft_angle(void) {
    return qfp_fmul((float)g_encoder.dir_, get_angle());
}

//* Used in TIM2 interrupt handler -- start
static float get_velocity(void) {
    float angle_curr, vel;

    // current angle
    angle_curr = get_angle();
    // angle change
    float d_angle = qfp_fsub(angle_curr, angle_prev);
    // velocity calculation
    vel = qfp_fdiv(d_angle, g_vel_ctrl.ctrl_rate);

    // prepare for next calculation
    angle_prev = angle_curr;

    return vel;
}

static float vel_prev = 0;
static float LPF_velocity(float v) {
    float vel_curr = qfp_fadd(qfp_fmul(0.9f, vel_prev), qfp_fmul(0.1f, v));
    vel_prev = vel_curr;
    return vel_curr;
}


static float get_shaft_velocity(void) {
    return qfp_fmul((float)g_encoder.dir_, LPF_velocity(get_velocity()));
}
//* Used in TIM2 interrupt handler -- end

static void encoder_gpio_init(void) {
    LL_GPIO_InitTypeDef GPIO_InitStruct = {0};

    // Enable GPIOB clock
    LL_APB2_GRP1_EnableClock(LL_APB2_GRP1_PERIPH_GPIOB);

    // Encoder CS pin Setting
    LL_GPIO_SetOutputPin(ENCODER_GPIO_PORT, ENCODER_CS_PIN);
    GPIO_InitStruct.Pin        = ENCODER_CS_PIN;
    GPIO_InitStruct.Mode       = LL_GPIO_MODE_OUTPUT;
    GPIO_InitStruct.Speed      = LL_GPIO_SPEED_FREQ_HIGH;
    GPIO_InitStruct.OutputType = LL_GPIO_OUTPUT_PUSHPULL;
    GPIO_InitStruct.Pull       = LL_GPIO_PULL_UP;
    LL_GPIO_Init(ENCODER_GPIO_PORT, &GPIO_InitStruct);
}

static void encoder_spi2_init(void) {
    LL_SPI_InitTypeDef SPI_InitStruct = {0};
    LL_GPIO_InitTypeDef GPIO_InitStruct = {0};

    /* Peripheral clock enable */
    LL_APB1_GRP1_EnableClock(LL_APB1_GRP1_PERIPH_SPI2);

    LL_APB2_GRP1_EnableClock(LL_APB2_GRP1_PERIPH_GPIOB);
    /** SPI2 GPIO Configuration
        => PB13   ------> SPI2_SCK
        => PB14   ------> SPI2_MISO
        => PB15   ------> SPI2_MOSI
    */
    GPIO_InitStruct.Pin              = ENCODER_SPI_SCK_PIN | ENCODER_SPI_MOSI_PIN;
    GPIO_InitStruct.Mode             = LL_GPIO_MODE_ALTERNATE;
    GPIO_InitStruct.Speed            = LL_GPIO_SPEED_FREQ_HIGH;
    GPIO_InitStruct.OutputType       = LL_GPIO_OUTPUT_PUSHPULL;
    LL_GPIO_Init(ENCODER_GPIO_PORT, &GPIO_InitStruct);

    GPIO_InitStruct.Pin              = ENCODER_SPI_MISO_PIN;
    GPIO_InitStruct.Mode             = LL_GPIO_MODE_FLOATING;
    LL_GPIO_Init(ENCODER_GPIO_PORT, &GPIO_InitStruct);

    SPI_InitStruct.TransferDirection = LL_SPI_FULL_DUPLEX;
    SPI_InitStruct.Mode              = LL_SPI_MODE_MASTER;
    SPI_InitStruct.DataWidth         = LL_SPI_DATAWIDTH_16BIT;
    SPI_InitStruct.ClockPolarity     = LL_SPI_POLARITY_LOW;
    SPI_InitStruct.ClockPhase        = LL_SPI_PHASE_2EDGE;
    SPI_InitStruct.NSS               = LL_SPI_NSS_SOFT;
    SPI_InitStruct.BaudRate          = LL_SPI_BAUDRATEPRESCALER_DIV8;
    SPI_InitStruct.BitOrder          = LL_SPI_MSB_FIRST;
    SPI_InitStruct.CRCCalculation    = LL_SPI_CRCCALCULATION_DISABLE;
    SPI_InitStruct.CRCPoly           = 10;
    LL_SPI_Init(SPI2, &SPI_InitStruct);

    // enable spi2
    LL_SPI_Enable(SPI2);
}

#include "foc.h"
#include "foc_app.h"
#include "pid.h"
void encoder_reset(void) {
    rotation_turns_angles = 0.0f;
    raw_angle_data_prev = (float)read_raw_angle();
    LL_mDelay(5);
    angle_prev = get_angle();
    LL_mDelay(5);
    g_foc.state_.shaft_speed = get_velocity(); // must be zero
    LL_mDelay(5);
    g_foc.state_.shaft_angle = get_shaft_angle();
    // Set current shaft angle as the target angle.
    // So the motor can stop after motion mode being switched.
    g_ang_ctrl.target_angle  = g_foc.state_.shaft_angle;
    g_vel_ctrl.target_speed  = 0.0f;

    // app
    g_foc_app.normal_.torque_ctrl_.target_torque  = 0.0f;
    g_foc_app.rebound_.rebound_angle_             = g_foc.state_.shaft_angle;
    g_foc_app.rebound_.torque_ctrl_.target_torque = 0.0f;
    g_foc_app.ratchet_.torque_ctrl_.target_torque = 0.0f;
}
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

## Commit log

2023-07-16 feat: basic project template created
    test TIM1 PWM and validate the control logic; give up proteus simulation; use logic analyzer to validate software.
    [stlink.cfg]
2023-07-16 feat: create hardware project
    [foc.SchDoc, foc_pcblib.PcbLib, foc_schlib.SchLib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]
2023-07-17 feat: finish board design(not checked) and update README.md
    [foc.PcbDoc, foc.SchDoc, foc_pcblib.PcbLib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]
2023-07-17 fix: delete redundant line in driver sch
    [foc.SchDoc]
2023-07-17 fix: fix mistakes in sch and generate gerber files
    [foc.PcbDoc, foc.SchDoc, foc_schlib.SchLib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]
2023-07-17 feat: update cmake content; add spi1; update tim1
    remove Startup folder and create STARTUP_ASM symbol to indicate startup asm file; insert spi1 and update tim1 settings
2023-07-18 feat: add SC60228DC driver and update SPI settings
    Further check to SC60228DC will be done if the hardware gets into ready.
2023-07-18 refactor: refactor encoder.h codition macro value
2023-07-19 feat: add qfplib-m3 float-point library
    use qfplib to optimize encoder calculation but haven't test it
2023-07-19 feat: qfplib-m3 test pass and add vofa+ components
    I can't ensure the vofa+ can work normally because my CH340 seems to be broken. It needs further checking.
    [encoder.c, encoder.h, foc.ioc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]
2023-07-20 feat: add oled init code and refactor spi and gpio structure
    merge the gpio and spi init into the specific functional files
2023-07-21 fix: fix oled display problem and confirm the right output of uart
    remove spi1 dma and add busy check of spi data sending
    [oled.c, vofa_usart.c]
2023-07-21 refactor: reconstruct pwm configuration and add bldc tests
    move TIM1 configurations into bldc_config.c and add bldc_test.c file to test motor performance; add void to functions without any parameters
2023-07-21 fix: fix config error of usart rx dma and sytax error of bldc test
    [bldc_config.c, bldc_test.c, vofa_usart.c]
2023-07-22 fix: fix problems in encoder
    fix spi transmission problem in encoder and add test function, but not fully check the functionality of encoder becasue I forget to buy magnectic!
    [main.SchDoc, miniFOC2022.PcbLib, miniFOC2022.SchLib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]
2023-07-22 refactor: remove encoder in main.c
2023-07-24 feat: add current sense monitor but the adc configurations have been done
2023-07-25 feat: current_monitor can obtain data but not normally updates it
2023-07-25 fix: fix NbData size to 4 bytes in current_monitor.c
    [current_monitor.c]
2023-07-25 fix: fix adc reg bank number in current_monitor.c
    [current_monitor.c]
2023-07-25 fix: NbData should be equal to the DataSize * num
    [current_monitor.c]
2023-07-25 fix: change TIM2 to TIM3 for ADC ext trigger source
    [current_monitor.c, foc.ioc]
2023-07-25 fix: fix ADC configuration problem and add current sense monitor
    [bldc_test.c, current_monitor.c, current_monitor.h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]
2023-07-26 feat: add oled base code and change OLED_CS pin
2023-07-28 fix: fix encoder angle read error, vel calculation still gets wrong
    [encoder.c, encoder.h]
2023-07-28 feat: add printf for GCC compiler version
2023-07-28 refactor: use struct to manage foc and encoder
    delete setvbuf function in vofa_usart.c, printf must end with '\n'
2023-07-28 fix: remove motor state
    [foc.c]
2023-07-28 feat: add sensor alignment code and fix printf ouput bug
    [encoder.c, encoder.h, foc.c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]
2023-07-28 fix: change printf radian angle to degree unit (float to int)
    [foc.c, vofa_usart.c]
2023-07-28 fix: update SENSOR_ALIGN_VOLTAGE; extends e_angle steps in sensor alignment
    [foc.c]
2023-07-29 refactor: velocity calculation seems to be abnormal, prepare to use freeRTOS to solve it.
2023-07-29 fix: Use TIM2 10KHz interrupt to fix the encoder velocity calucation error
    [current_monitor.c, encoder.c, encoder.h]
2023-07-29 feat: add velocity loop control but still exist some flaws
    The motor jitters frequently!
    [encoder.c, encoder.h, foc.c]
2023-07-29 fix: add derivative part in PID_velocity control(remove jitter)
    [foc.c]
2023-07-29 fix: fix motor jump problem when motion type is changed
    [encoder.c, encoder.h, foc.c]
2023-07-29 fix: Remove integral part in Angle Control. Only proportional part is left.
    Integral actually causes serious overshoot problem and affects the system response speed.
    [foc.c, vofa_usart.c]
2023-07-30 feat: add torque control and current feed back loop(trapped into the errors)
    I think I haven't get the right phase seqeuence of current. The motor can rotate well under voltage control, however, current control not.
    [current_monitor.c, current_monitor.h, encoder.c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]
2023-07-30 docs: add notes and recover voltage feedback mode
2023-07-31 fix: add notes and fix the motor bugs
    [foc.c]
2023-07-31 feat: add q d monitor and update align sensor function
2023-07-31 fix: do some changes in cuurent loop
    fix current sensor bugs, but suitable PID parameters for current loop haven't benn found.
    [current_monitor.c, foc.c, vofa_usart.c]
2023-07-31 perf: get some progress in current loop adjustment
2023-07-31 refactor: switch serial output to angle, speed and electrical angle
2023-07-31 feat: add ratchet mode under torque control
2023-08-01 fix: fix and optimize easing functions
    [easing.c]
2023-08-02 fix: fix mistakes found in easing.c
    [easing.c]
2023-08-03 refactor: invalid the irrelevant functions, which about motor control
2023-08-03 fix: fix bugs in gui and refactor the tween and menu list definitions
    gui_init needs to declare the pages as the global variables. Otherwise, the lifetime of these varibles will end if this init function exit.
    [gui.c, tween.c]
2023-08-03 fix: fix easing function display errors; update font style; fix download flash size
    [stlink.cfg]
2023-08-03 feat: add stm32f103xx.svd file
2023-08-04 feat: add _printf_float ld option; add OLED PID control slider
2023-08-04 fix: clear display area before showing the slider in PID gui
    [gui.c]
2023-08-04 feat: add torque mode switch command and do motor and OLED integration test
2023-08-04 feat: add motor mode switch option in OLED gui
2023-08-04 feat: add animation for motor running and make associated configs
2023-08-04 fix: fix torque_ratchet_mode error
    add shaft angle normalization function
2023-08-04 perf: optimize dead erea of angle control pid; update OLED main UI
2023-08-05 feat: update voltage control with current estimation and Back-EMF compensation
2023-08-05 feat: add torque rebound mode in foc_app.c and refactor torque pid factor
2023-08-06 feat: current loop can work fine at high speed, but not low speed
2023-08-07 perf: reconstruct gui to support app mode switch
2023-08-07 feat: add damp mode under torque control; update MainUI annimation
    The Kd value in rebound mode can increase the damp intensity; The main UI annimation will change following the actual angle
2023-08-07 refactor: add a new marco to control info output and fix current resolution value
    [current_monitor.h]
2023-08-07 docs: add motor info in README.md
2023-08-07 refactor: decrease current loop to 5 KHz and update damp command
2023-08-07 feat: Add HPF in current sense and fix some bugs
    HPF filters out the 15 ms noise obtained from ADC sampling; fix torque normal mode syntax problem that cause no torque output; enhance the SVPWM calculation
    [current_monitor.c, current_monitor.h, foc.c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]
2023-08-07 fix: fix SVPWM errors and remove some debug code; current loop not done
    The current loop seems always out of control (Id and Iq have coupling relationship)
    [current_monitor.c, foc.c]
2023-08-08 feat: add another current sense component; motor can not rotate normally now
2023-08-08 test: The encoder seems to be damaged?
    [current_monitor.c]
2023-08-08 feat: add three phase current process code
2023-08-10 fix: set correct current phases
    [current_monitor.c, current_monitor.h, foc.c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]
2023-08-10 fix: fix incorrect TIM3 config; ajust foc state update way; switch to three phases current monitor
    [current_monitor.c, current_monitor.h, foc.c]
